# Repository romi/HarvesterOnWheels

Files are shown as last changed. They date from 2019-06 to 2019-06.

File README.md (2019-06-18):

# HarvesterOnWheels

**Harvesting mixed salads is a painful task when done by hands and there are existing tools to ease the cutting of these plants. Hacking on this, we propose to build a mixed salad harvester. We make the blade larger so that it can harvest all salads in one pass on the the culture bed and we put the machine on wheels so that it is easy to handle.**

design files for the harvester on wheels :
* /2d: dxf files for laser cut parts
* /3d: f3z and stp design files
* /drawing: design files as drawing with measures

## Bill of materials

### Wheels

|N°||Designation ETRTO|Qty|
|---|---|---|---|
|1|Front wheel|47-203|2|
|2|Rear wheel|47-406|2|

### Frame

|N°|Designation|Length|Qty|
|---|---|---|---|
|1|Rear fork||4|
|2|Square tube||2|
|3|Profile 20x20 |1000|2|
|4|Profile 20x20 |1106|2|
|5|Profile 20x20 |960|2|
|6|Profile 20x20 |1146|1|
|7|Profile 20x20 |640|4|
|8|Profile 20x20 |757|2|
|9|Profile 20x20 |106|4|
|10|Angle Brackets||2|

### Harvesting tool

|N°|Designation|Qty|
|---|---|---|
|1| Greens Harvester plate (drill side)|1|
|2|Greens Harvester plate (other side)|1|
|3| Flange bearing 10mm (KFL000)|2|
|4|Threaded shaft M10 x 1000|1|
|5|Blade Plate 1| 1|
|6|Blade Plate 2|1|
|7|Blade Plate 3|1|
|8|Butcher bandsaw blade|1|
|9| Angle brackets|2|
|10| Rope 340 | 100|
|11| Wire 3000 |1|
|12| Outdoor fabric||

## Assembly instructions

### Frame

* Where the profile make a right angle use fastening bracket for asembly (36 of them).
* For the other assembly points use joints (8 of them).
* Attach the rear fork with post-assembly M5 fastening bolts and flanged nuts.
* Drill holes depending on the wheels and angle brackets and fix the square tubes with angles brackets.

### Harvesting tool

* Cut side plates at the corner on each side of the Greens Harvester.
* Attach pieces of rope to the wire and roll it around the threaded shaft.
* Attach side plates and blade plates 1, 2, 3 with angle brackets.
* Attach the side plates to the frame with post-assembly M5 fastening bolts and flanged nuts.
* Sew the fabric as shown on the drawing.
* Attach the fabric to the frame and under the blade plate.
* Insert the butcher blade and link it to the side plate on the drill side.



This work is licensed under the [Creative Commons license](https://creativecommons.org/licenses/by/4.0/)

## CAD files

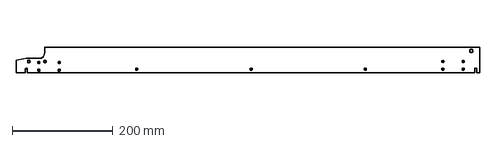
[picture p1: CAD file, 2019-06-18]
2d/Blade_plate_1.dxf
918.6 x 50.0 mm

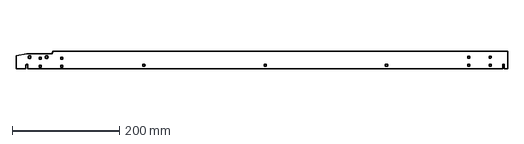
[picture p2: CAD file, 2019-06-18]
2d/Blade_plate_2.dxf
918.6 x 33.5 mm

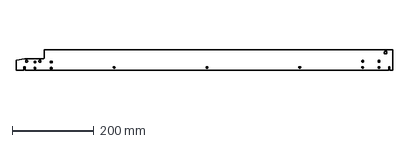
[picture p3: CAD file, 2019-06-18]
2d/Blade_plate_3.dxf
918.6 x 50.0 mm

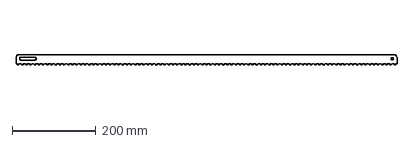
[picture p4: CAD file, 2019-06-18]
2d/Butcher_blade.dxf
910.0 x 25.0 mm

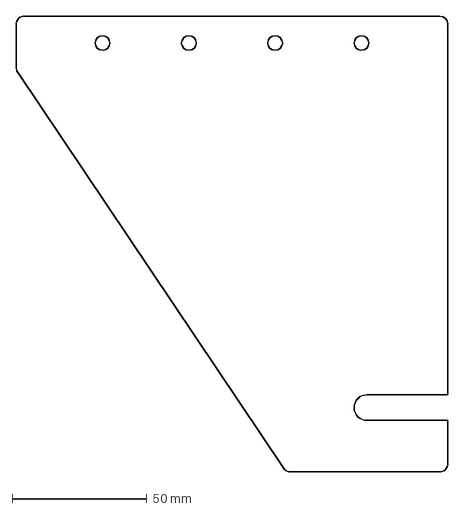
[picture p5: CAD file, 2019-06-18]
2d/Rear_fork.dxf
160.0 x 169.0 mm

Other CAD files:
3d/Harvester_on_wheels.f3z

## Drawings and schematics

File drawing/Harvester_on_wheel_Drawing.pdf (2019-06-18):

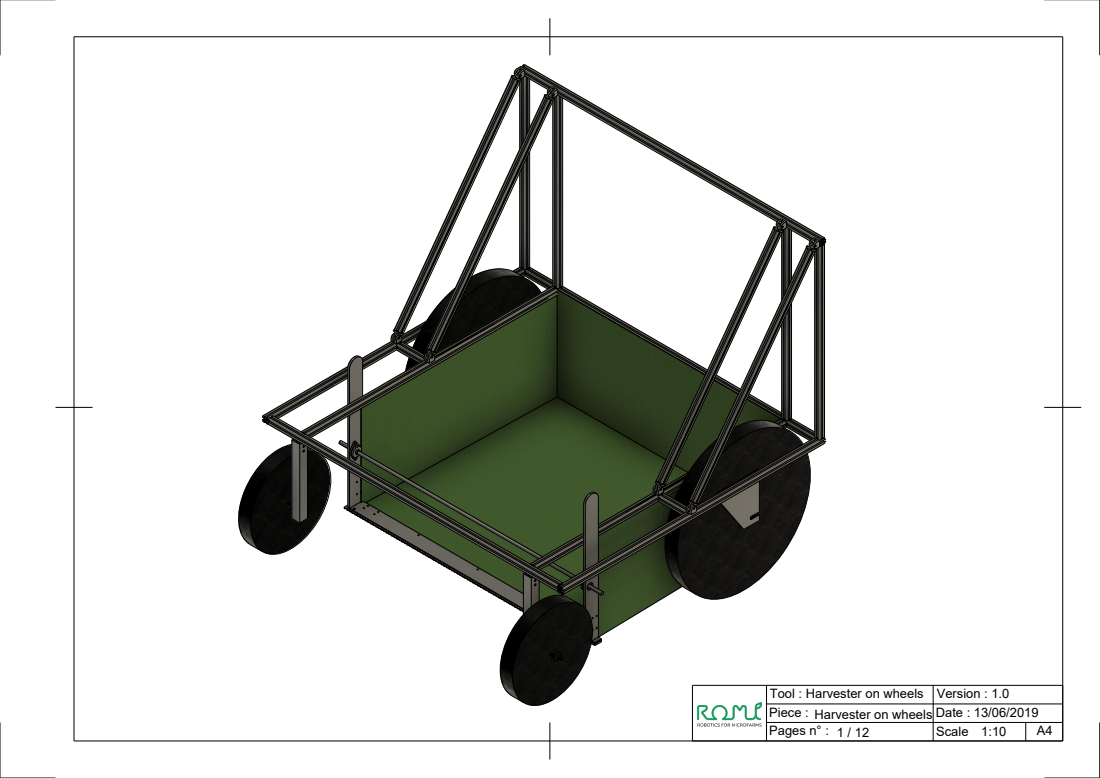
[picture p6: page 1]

Tool : Harvester on wheels | Version : 1.0
Piece : Harvester on wheels | Date : 13/06/2019
Pages n° : 1 / 12 | Scale 1:10 | A4

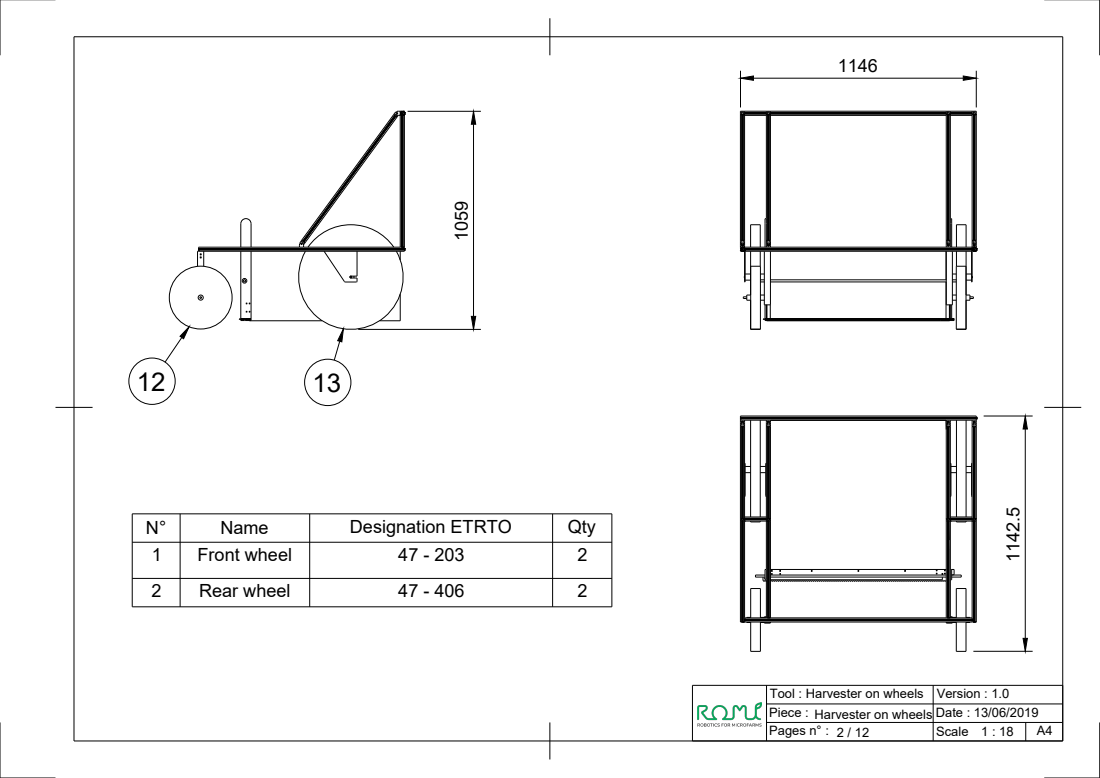
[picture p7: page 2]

Harvester on wheels 1059

N° | Name | Designation ETRTO | Qty
1 | Front wheel | 47 - 203 | 2

2 | Rear wheel | 47 - 406 | 2

Tool : Harvester on wheels | Version : 1.0
Piece : | Date : 13/06/2019

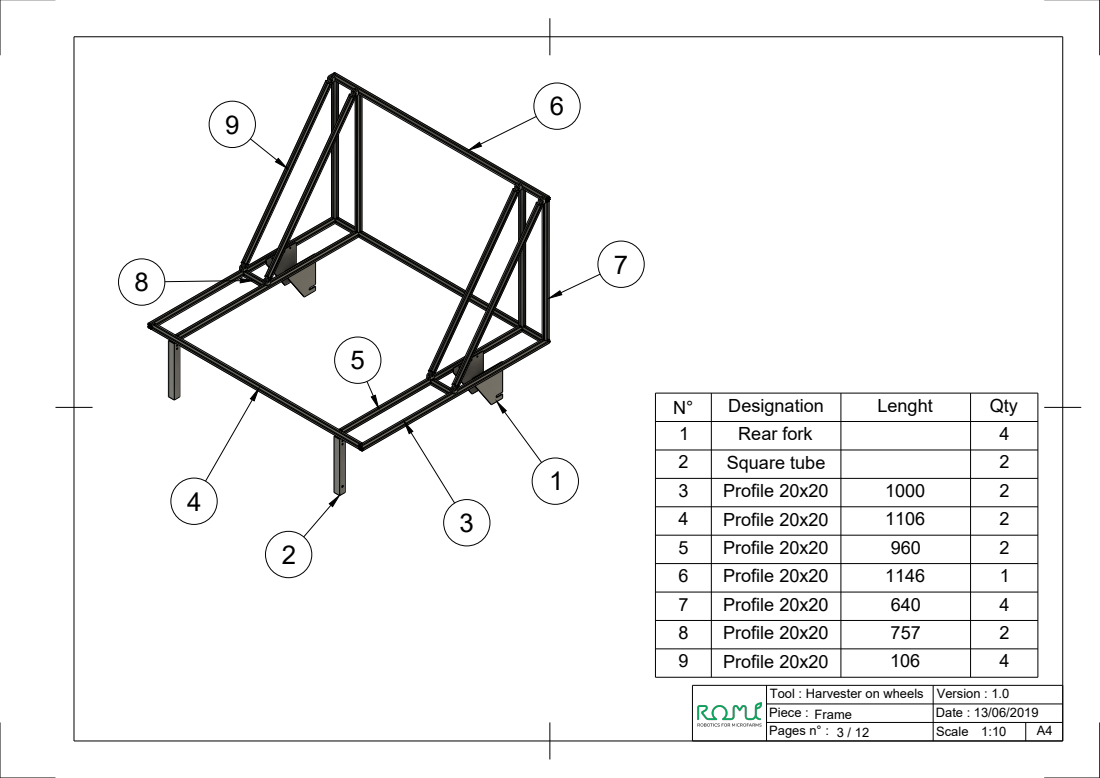
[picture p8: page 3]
Designation; Lenght; Qty 1; Rear fork; Square tube; Profile 20x20

Tool : Harvester on wheels | Version : 1.0
Piece : Frame | Date : 13/06/2019

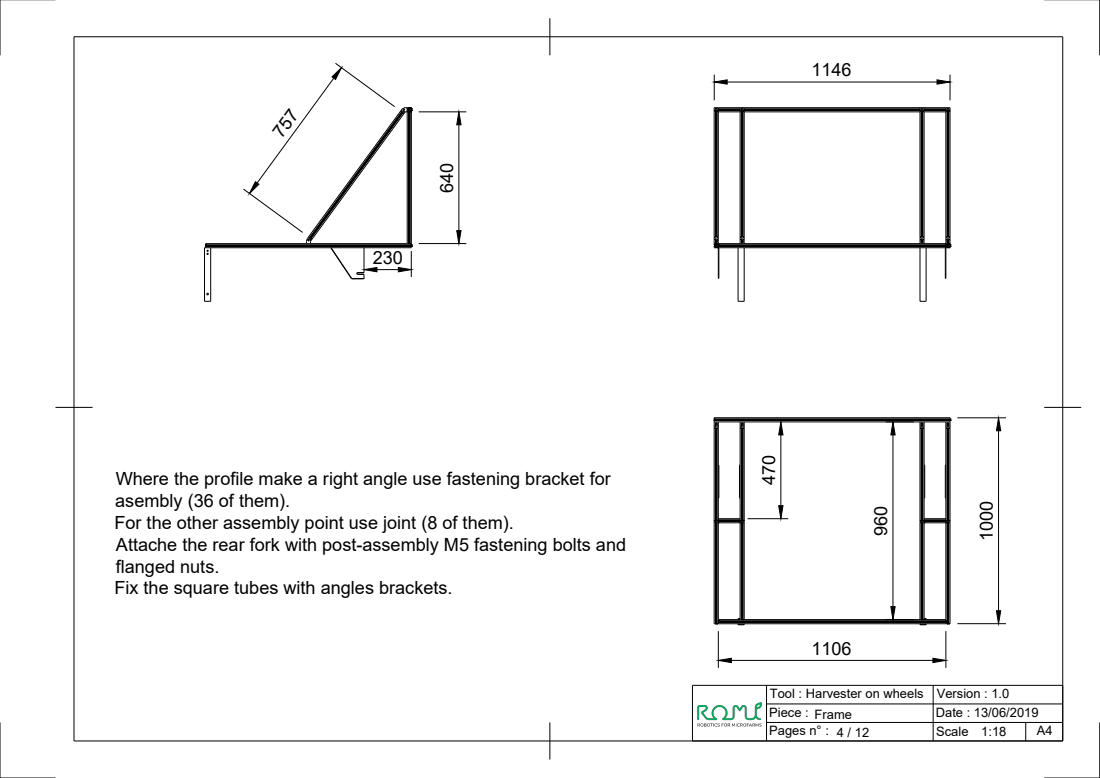
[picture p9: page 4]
Where the profile make a right angle use fastening bracket for

asembly (36 of them).
For the other assembly point use joint (8 of them).
Attache the rear fork with post-assembly M5 fastening bolts and
flanged nuts.
Fix the square tubes with angles brackets.

Tool : Harvester on wheels | Version : 1.0
Piece : Frame | Date : 13/06/2019

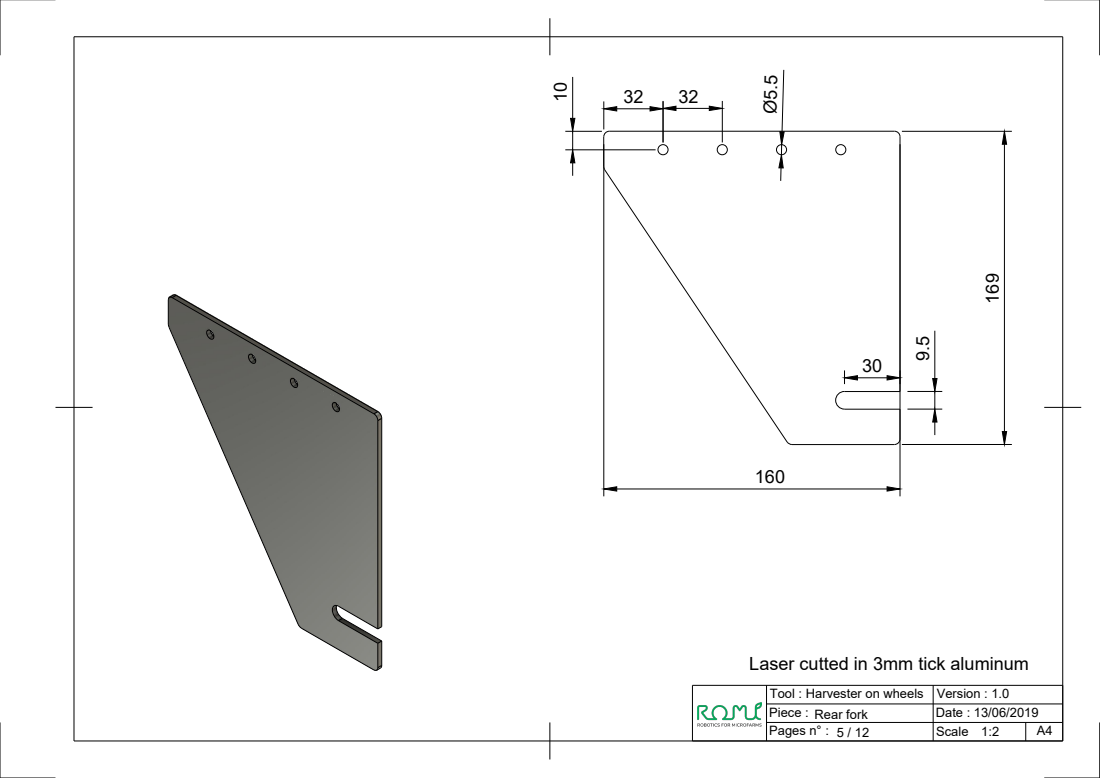
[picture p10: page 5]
Laser cutted in 3mm tick aluminum Ø5.5

Tool : Harvester on wheels | Version : 1.0
Piece : Rear fork | Date : 13/06/2019

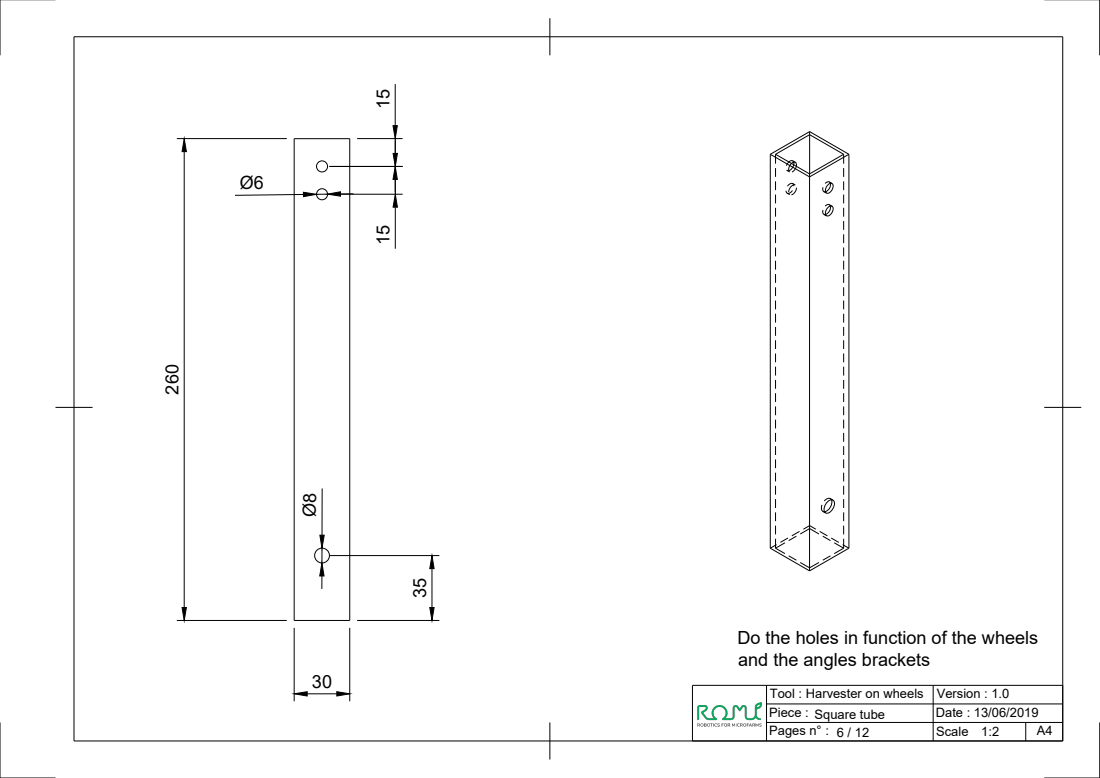
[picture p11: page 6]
Square tube 260

Do the holes in function of the wheels
and the angles brackets

Tool : Harvester on wheels | Version : 1.0
Piece : | Date : 13/06/2019

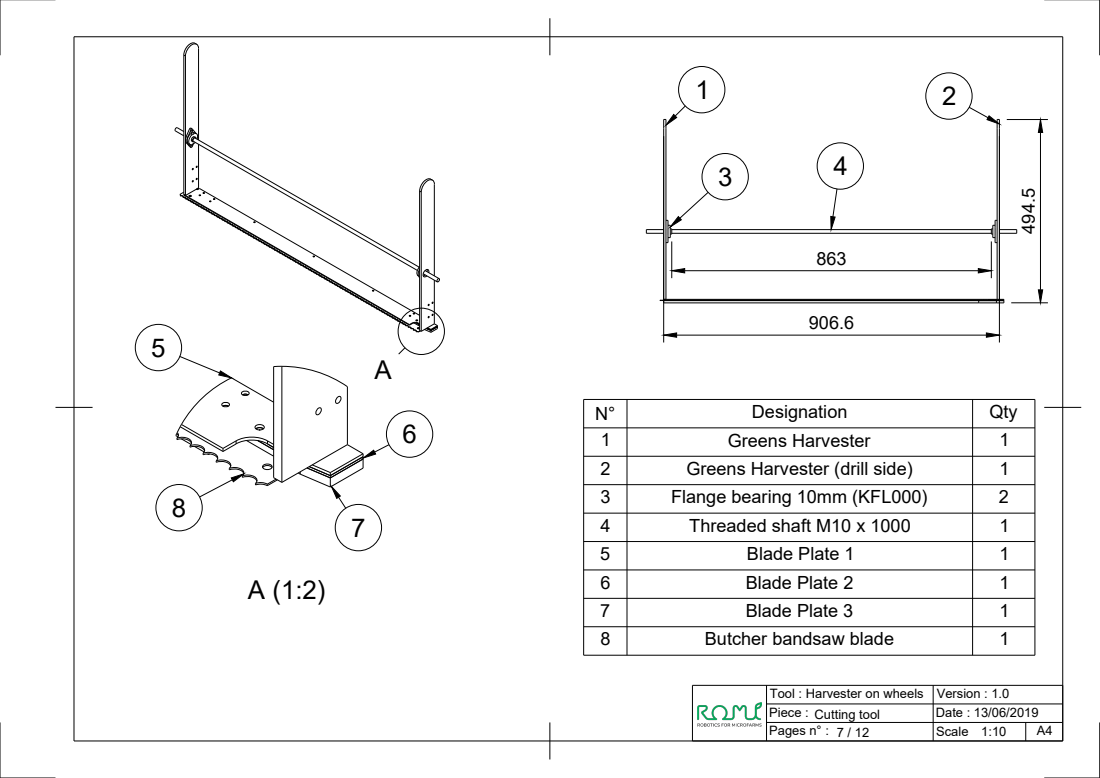
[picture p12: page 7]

N° | Designation | Qty
1 | Greens Harvester | 1
2 | Greens Harvester (drill side) | 1
3 | Flange bearing 10mm (KFL000) | 2
4 | Threaded shaft M10 x 1000 | 1
5 | Blade Plate 1 | 1
6 | Blade Plate 2 | 1
7 | Blade Plate 3 | 1
8 | Butcher bandsaw blade | 1

Tool : Harvester on wheels | Version : 1.0
Piece : Cutting tool | Date : 13/06/2019

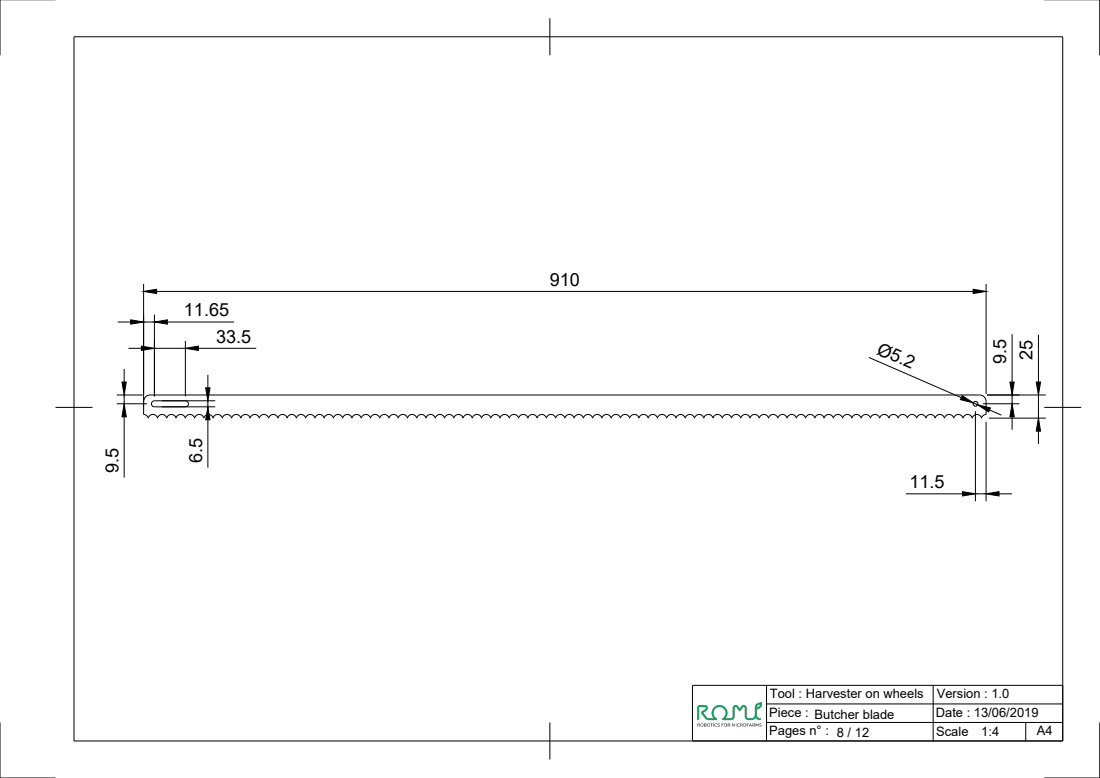
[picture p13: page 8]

Tool : Harvester on wheels | Version : 1.0
Piece : Butcher blade | Date : 13/06/2019

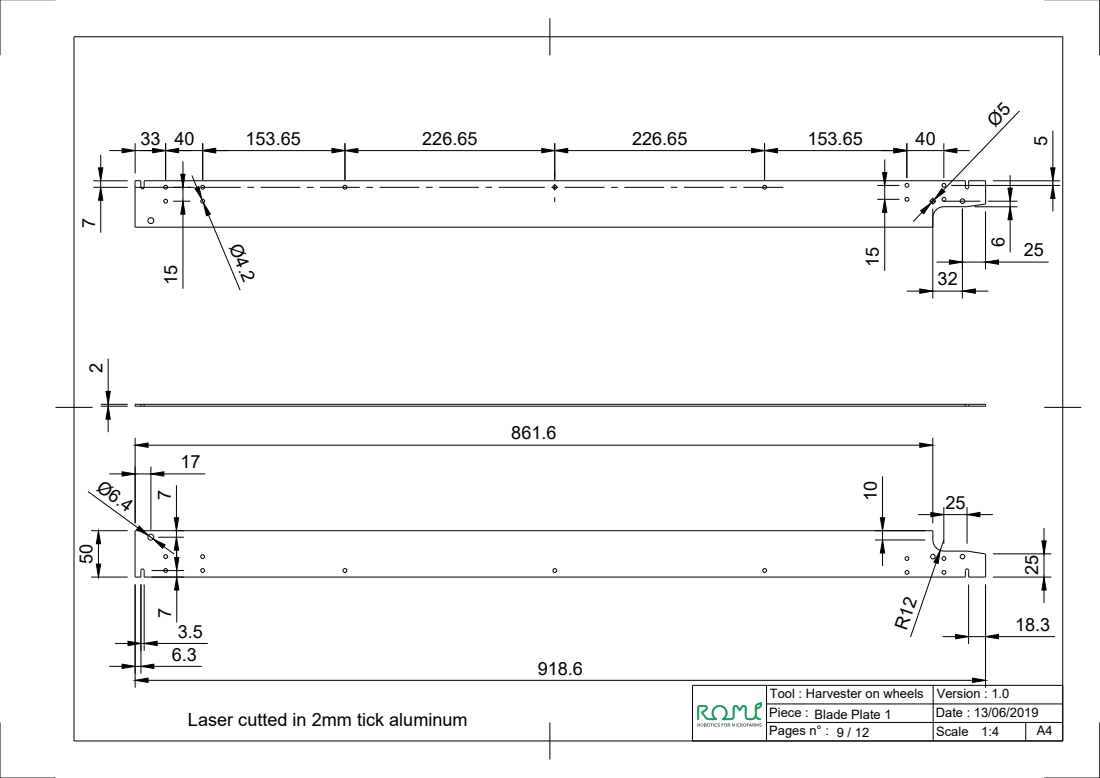
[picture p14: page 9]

Tool : Harvester on wheels | Version : 1.0
Piece : Blade Plate 1 | Date : 13/06/2019

Laser cutted in 2mm tick aluminum

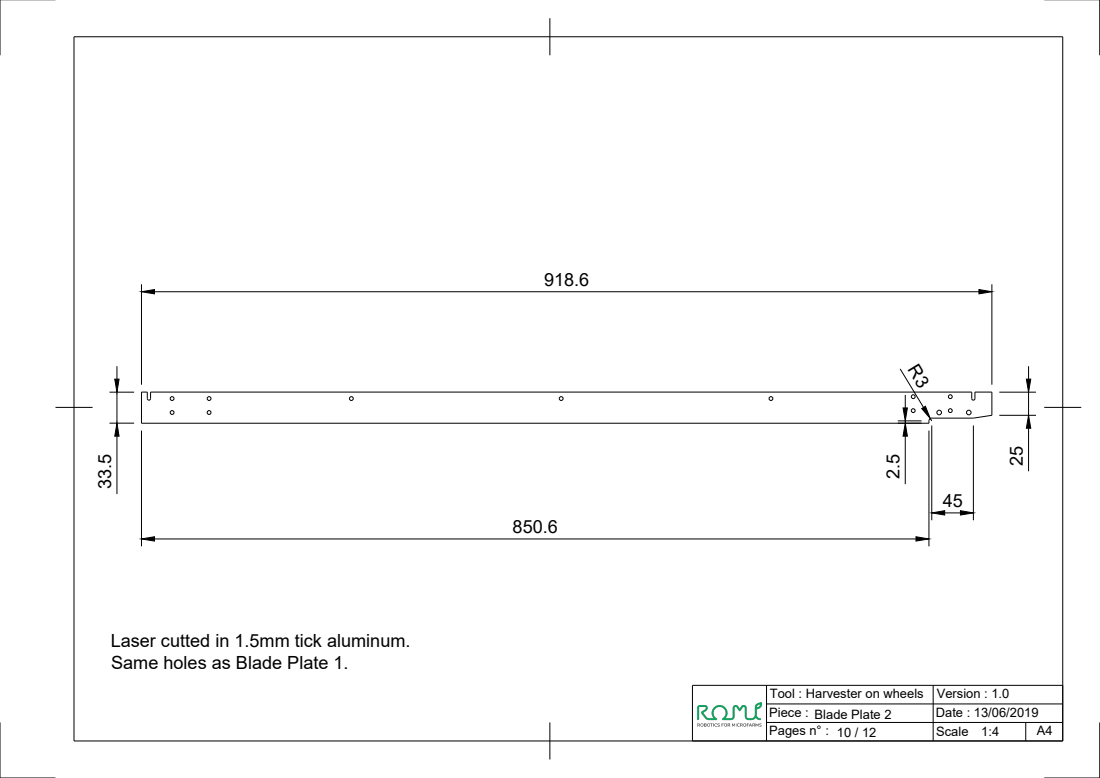
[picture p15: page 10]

Same holes as Blade Plate 1. 33.5

Laser cutted in 1.5mm tick aluminum.

Tool : Harvester on wheels | Version : 1.0
Piece : Blade Plate 2 | Date : 13/06/2019

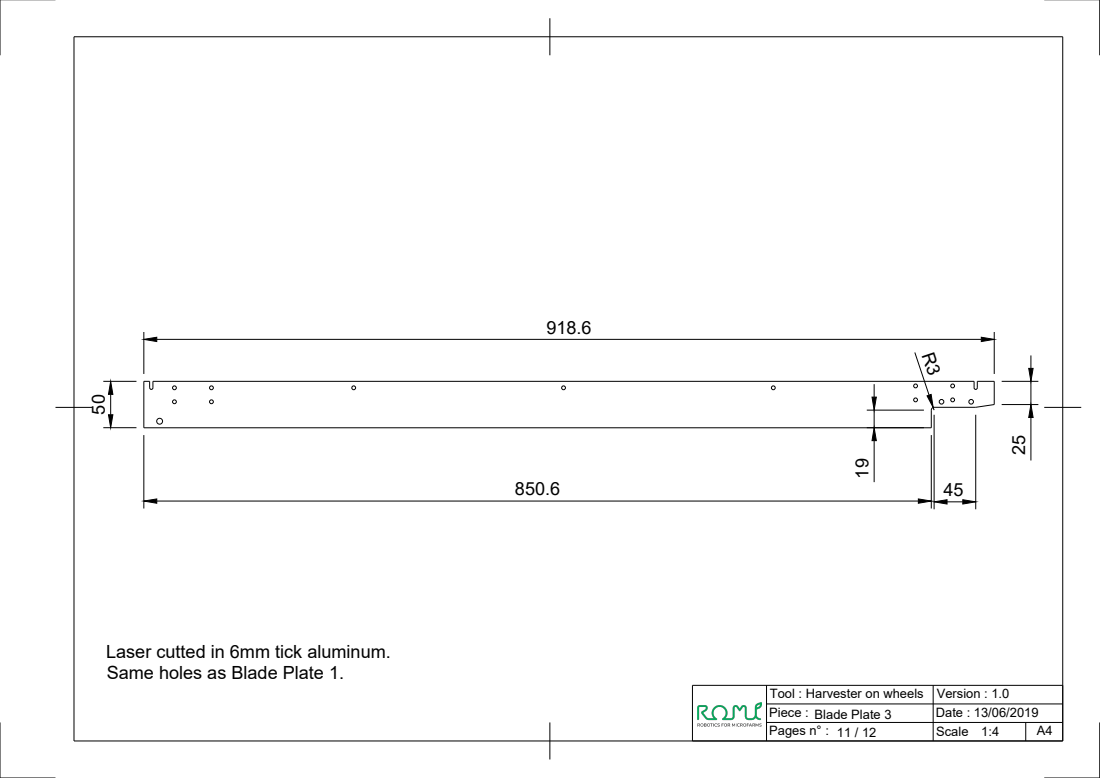
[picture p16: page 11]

Same holes as Blade Plate 1. 50

Laser cutted in 6mm tick aluminum.

Tool : Harvester on wheels | Version : 1.0
Piece : Blade Plate 3 | Date : 13/06/2019

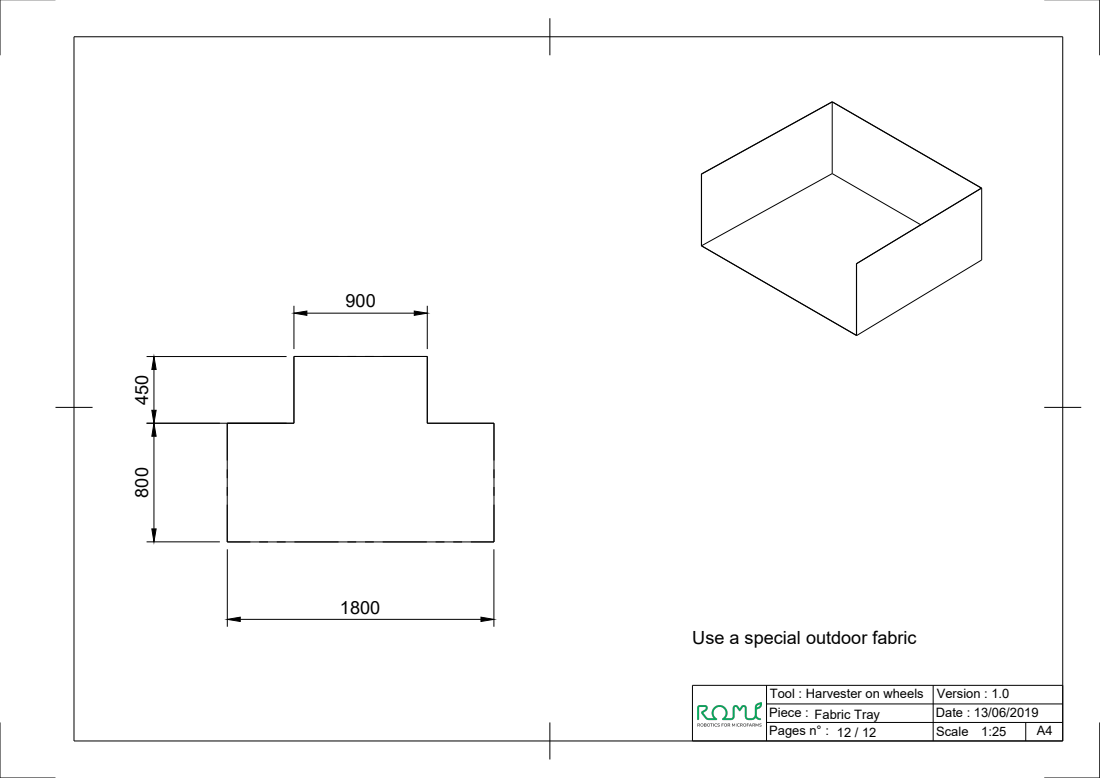
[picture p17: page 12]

Use a special outdoor fabric

Tool : Harvester on wheels | Version : 1.0
Piece : Fabric Tray | Date : 13/06/2019

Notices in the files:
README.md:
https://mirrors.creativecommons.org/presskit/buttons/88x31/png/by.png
